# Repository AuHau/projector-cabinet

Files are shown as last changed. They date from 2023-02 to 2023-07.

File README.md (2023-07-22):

# UST Projector cabinet

> DIY "TV" cabinet project housing a hidden motorized screen and UST (ultra-short-throw) projector in motorized drawer.

Demo vide (https://www.youtube.com/watch?v=b7_Dzy0piuk)

## Features

 - "One-press" setup of the home cinema for watching
 - Home Assistant integration
 - Temperature sensor for monitoring the projector's temperature
 - Fans for cooling the projector
 - Collision monitoring of the drawer
 - OTA firmware updates
 - Remote logging to syslog target

## About the project

From my childhood I have dreamed of my own home cinema. About two years ago I have 
decided to embark on an adventure to slowly built it. Since we lived at that moment 
in small flat and planned to move some time soon, creating dedicated "room based" setup was not an 
option. It was around that time that I discovered Ultra Short Throw (UST) projectors
that would match all my requirements and slowly an idea started to grow in my head:

_What if I could place it into a cabinet and have very clean setup with all the components hidden when not using?_

And that is what I have started to work on over weekends and evenings for past 9 months.

Here I plan to share my final design and firmware code for anybody who would like to replicate (and possibly improve on) my work.
I won't be detailing it to the "step-by-step" guide, but leave resources here for people who
know what to do and how to do it.

**I have to warn you though. The project is very tailored to the specific components that I used and describe
later. Any deviation from those components require proper modification of other parameters!**

**Every centimeter makes big difference in the UST projector's screen size and position!**

## Components

 1. UST Projector: [Samsung LSP7T](https://www.samsung.com/uk/projectors/the-premiere/the-premiere-smart-4k-uhd-laser-projector-sp-lsp7tfaxxu/)
 1. Tensioned Floor Screen for UST projects: [Vividstorm S Pro 110"](https://www.vividstorm.eu/products/Vividstorm-S-Pro-110-Electric-Acoustically-Transparent-Floor-Screen-p298146472)
 1. AVR: [Denon X3800H](https://www.denon.com/en-us/product/av-receivers/avr-x3800h/300609-new.html) 
 1. Speakers: 5+1(subwoofer) + 2("Atmos" drivers) from JAMO S809 series
 1. Custom built cabinet from oak
 1. Linear actuator with potentiometer for positional feedback
 1. Control logic board with ESP32

### Cabinet

I am still novice when comes to wood working, so I have decided to leave the build of the
cabinet to my friend cabinetmaker. Therefore, I have design it and modeled it in Fusion 360 
as it was crucial to get the dimensions right because UST projector's viewports are very sensitive 
to any even small deviation and I wanted to obviously maximize the screen's utilization.

This is a render of the model: 

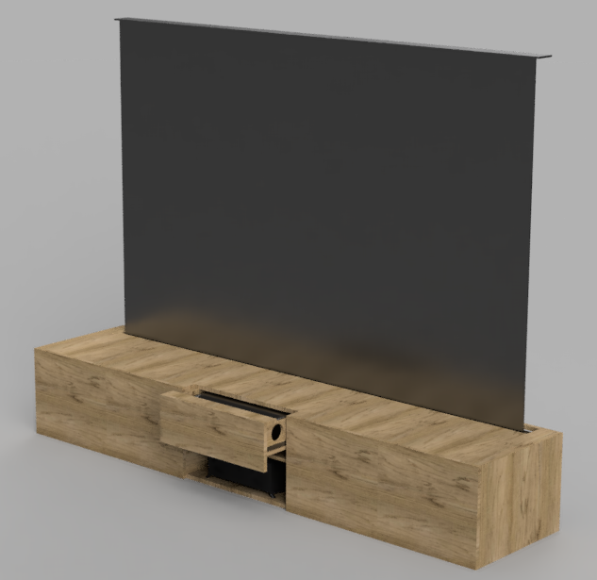
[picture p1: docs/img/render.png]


You can find the Fusion model as file [here](docs/cabinet_model.f3z) or as online model [here](https://uhlir.autodesk360.com/g/shares/SH9285eQTcf875d3c5399135f607261bca4c).
But be aware it is not complete model that could be used as blueprint
for recreating the cabinet! It served more like a mock to understand the dimension requirements.

### Electronics

The brain of the cabinet is custom build circuit around ESP32. I have decided
to program its firmware with MicroPython as Python is close to my heart. The 
circuit serves as integration point of several things:

 - controlling the linear actuator that opens/closes the projector's cabinet
 - controlling USB radio stick of the motorized screen (it works in simple way, if there is power going to the stick than screen is opened, otherwise it closes)
 - controlling the additional PC Fans mounted in the back of the projector's cabinet as otherwise the projector overheats
 - exposing temperature information about the projector

Originally my design goal was to have self-contained circuit. Later on, I have
deviated from this goal as I have decided to scratch my original approach for 
triggering openning/closing the cabinet using monitoring of the AC power line
to the projector and doing decision based on the current passing through that line.

I have instead opted to expose the above functionalities as Home Assistant entities and use the Home Assistant integration to Samsung's Tizen 
that runs on the projector for triggering the proper actions. 
Unfortunately it is not so reliable as sometimes the events from Tizen are not triggered or are triggered multiple times.
I had version of the firmware that was ready for the current-sensing approach, so if you would be interested in that
have a look on [this commit](https://github.com/AuHau/projector-cabinet/commit/b25f13ab9c904240c6eca4cdfa69838080070a1d). 
But be aware even though it was functional, it was not properly tested and finished.

The final schema which includes also the component for measuring the projector's line current mentioned above is here:

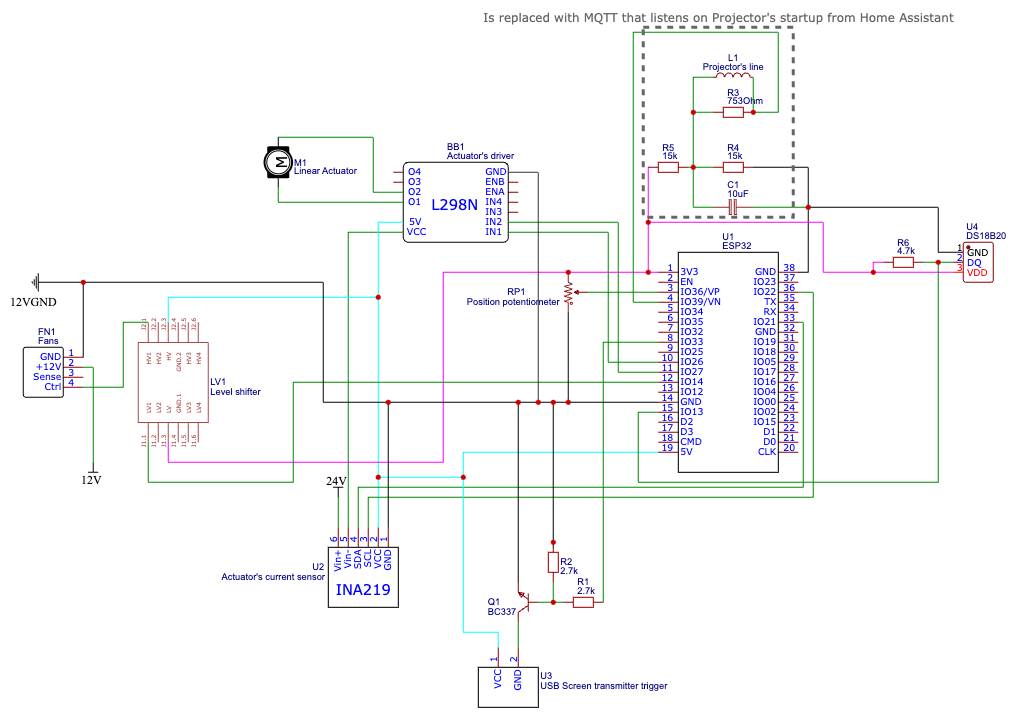
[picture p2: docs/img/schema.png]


You can download its export from EasyEDA [here](./docs/easda-schema.json).

Some pictures of prototyping and final assembly:

<table width="100%">
  <tr>
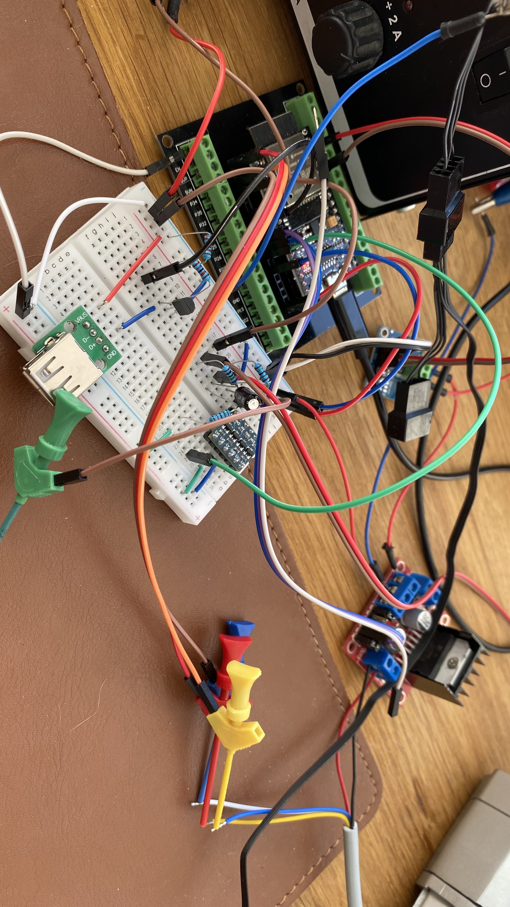
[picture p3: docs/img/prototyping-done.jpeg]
  <td width="50%">  </td>
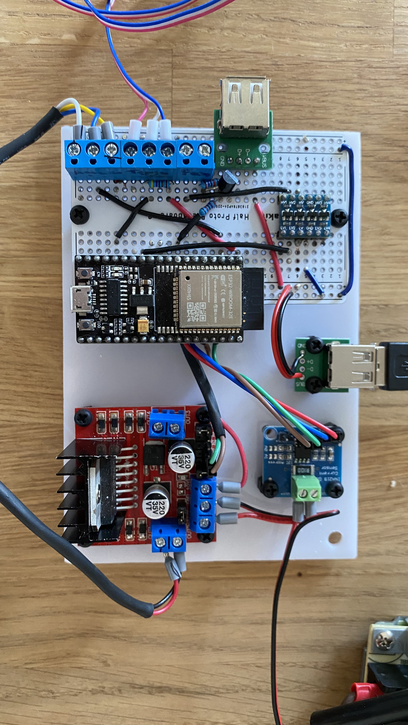
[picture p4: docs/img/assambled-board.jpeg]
  <td width="50%"> </td>
  </tr>
  <tr>
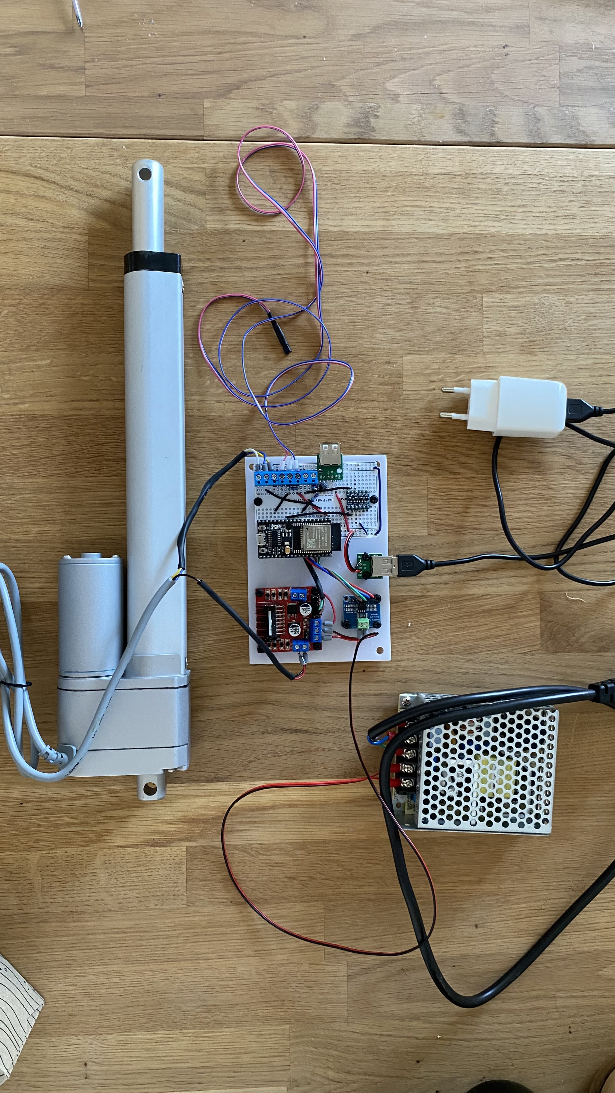
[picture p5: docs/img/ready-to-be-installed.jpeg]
  <td width="50%"></td>
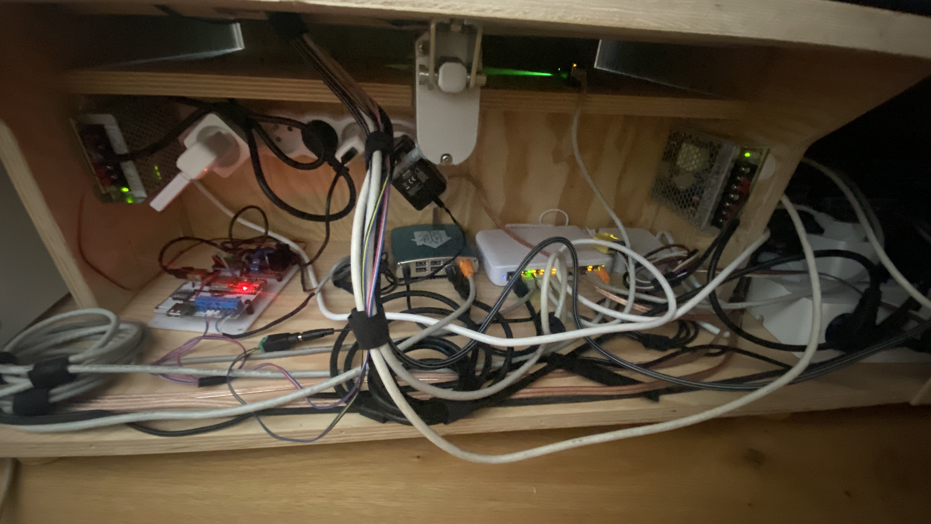
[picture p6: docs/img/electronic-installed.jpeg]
  <td width="50%"></td>
  </tr>
</table>

## Home Assistant

This project heavily relies on Home Assistant for orchestration and integration. Bellow you can see the overview and
capabilities that are exposed over Home Assistant:

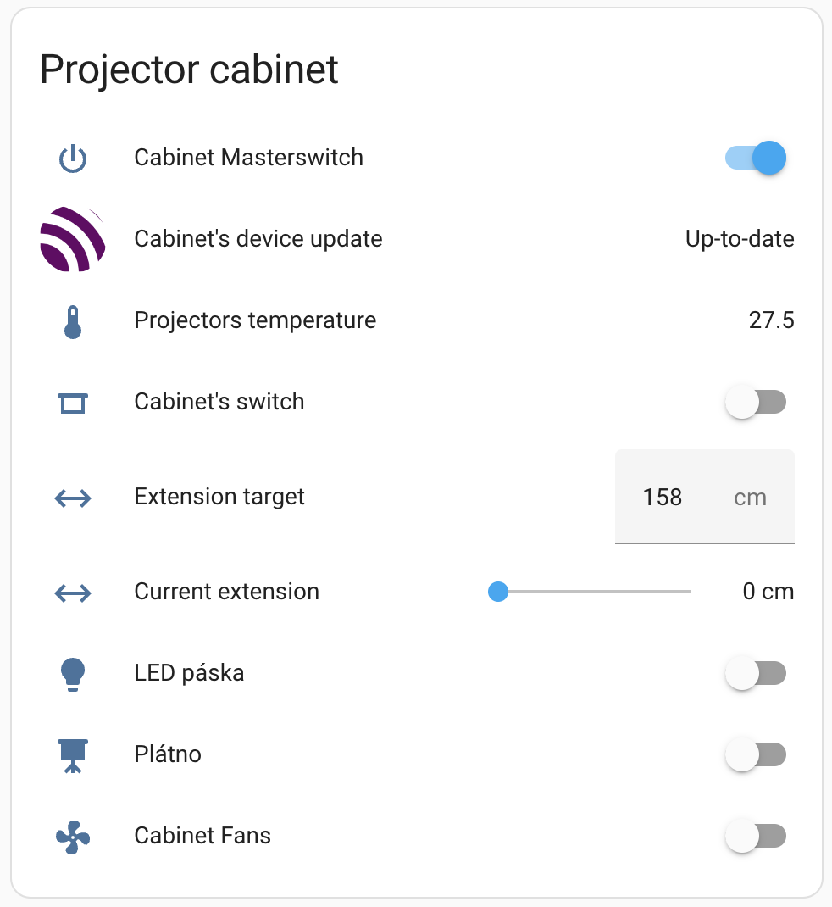
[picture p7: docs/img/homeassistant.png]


## Reproducing the project

As I said I won't provide "step-by-step" guideline here, but here are some pointers for reproducing this, mainly related
to firmware.

### Configuration

Fork this repo. The important configuration needs to be placed in `/app/secrets.py` file. This
file should not be commited (and is currently in `.gitignore`) as it contains sensitive configuration. This configuration
will be persisted over OTA updates. Content of this file shoudl be:

```python
# WiFi settings
WIFI_SSID = "" # YOUR WIFI NAME
WIFI_PASS = "" # YOUR WIFI PASSWORD

# MQTT settings
MQTT_BROKER = "" # NODE WHERE YOU RUN HOME-ASSISTANT'S MQTT
MQTT_USER = ""
MQTT_PASS = ""

# Syslog logging
SYSLOG_HOST = "" # NODE WHERE YOU RUN SYSLOG COLLECTOR
SYSLOG_PORT = ""
```

### OTA updates

OTA updates are sourced from GitHub Releases. For creating those there is Release-Please action which creates
Release PR that when you merge it create new release. With the new release a new firmware resource is build
with CI, which compiles the Python files `.py` into [`.mpy` files](https://docs.micropython.org/en/latest/reference/mpyfiles.html). 

For updating the firmware you need to press in Home Assistant "Install" button on the Firmware entity.

You need to point for the OTA updates to your forked repo in the `/main.py` file you need to tweak the `OTA_REPO` variable.

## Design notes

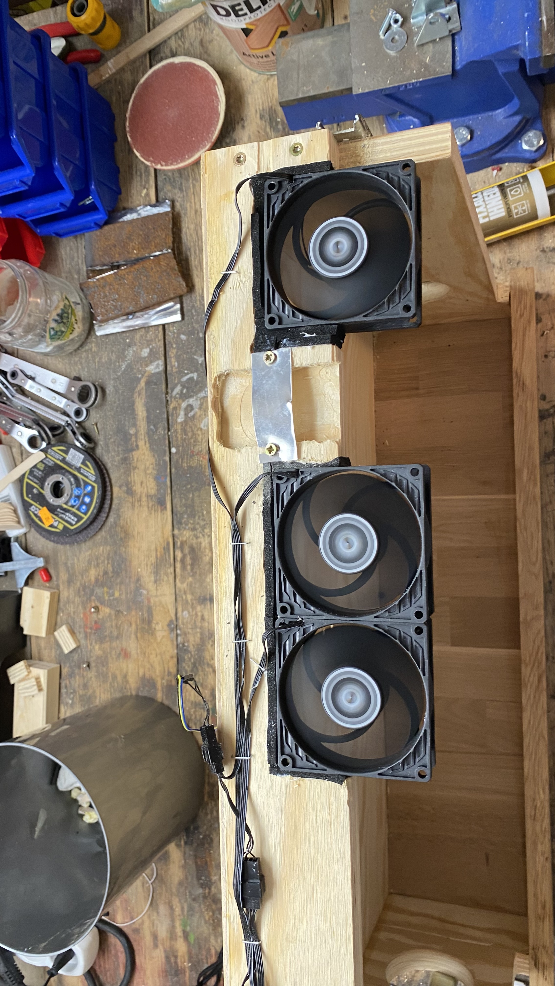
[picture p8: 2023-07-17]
docs/img/fans.jpeg

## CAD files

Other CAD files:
docs/cabinet_model.f3z

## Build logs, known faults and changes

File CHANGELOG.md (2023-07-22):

# Changelog

## [0.3.2](https://github.com/AuHau/projector-cabinet/compare/v0.3.1...v0.3.2) (2023-07-22)

### Bug Fixes

* some more fixing ([0126693](https://github.com/AuHau/projector-cabinet/commit/0126693fc49ac88e7b52665757672bb9edbba45f))
* traceback for unhandled exceptions ([87618a4](https://github.com/AuHau/projector-cabinet/commit/87618a41633968a7fd9db245ec9cdd786ce4bce1))

## [0.3.1](https://github.com/AuHau/projector-cabinet/compare/v0.3.0...v0.3.1) (2023-06-19)

### Bug Fixes

* underflow of fan pwm ([eb5e9b9](https://github.com/AuHau/projector-cabinet/commit/eb5e9b9d5d2ecf6da5a343ec5694fcccc4ab3049))

## [0.3.0](https://github.com/AuHau/projector-cabinet/compare/v0.2.1...v0.3.0) (2023-06-19)

### Features

* **mqtt:** expose actuator's extension ([5a29ce4](https://github.com/AuHau/projector-cabinet/commit/5a29ce446627cf0632ab04ef4f666a7cec7c00e0))

### Bug Fixes

* recover correct configuration when restarting after crash ([5ed0ff6](https://github.com/AuHau/projector-cabinet/commit/5ed0ff681734d7d25988c2870c71c69acecf9d1b))
* syslog format ([484e1cb](https://github.com/AuHau/projector-cabinet/commit/484e1cbc50b07813cca8b98dd84b1062b6938779))

## [0.2.1](https://github.com/AuHau/projector-cabinet/compare/v0.2.0...v0.2.1) (2023-06-18)

### Bug Fixes

* bugs ([7dee334](https://github.com/AuHau/projector-cabinet/commit/7dee334d7eafd5650619703c98dbe3d5649d6b00))

## [0.2.0](https://github.com/AuHau/projector-cabinet/compare/v0.1.5...v0.2.0) (2023-06-18)

### Features

* **mqtt:** extension target configuration ([f5e87b5](https://github.com/AuHau/projector-cabinet/commit/f5e87b5617057703612a36bc812b0418c790dd0a))
* **mqtt:** fans configuration ([5a57b42](https://github.com/AuHau/projector-cabinet/commit/5a57b42f79fea2eea04af359a79ac7d08bdff45d))

### Bug Fixes

* **fan:** off resets duty cycle ([2952681](https://github.com/AuHau/projector-cabinet/commit/2952681409744ba1f1e988e2f01610850ec01ed6))
* revert custom tar and fix tarfile ([b5f4f8b](https://github.com/AuHau/projector-cabinet/commit/b5f4f8b6b115490de6233753be86939c8b0f6fb9))

## [0.1.5](https://github.com/AuHau/projector-cabinet/compare/v0.1.4...v0.1.5) (2023-06-17)

### Bug Fixes

* use different tar compress ([04af35d](https://github.com/AuHau/projector-cabinet/commit/04af35d7a5fc833fdee7b87c0004e570961c3dae))

## [0.1.4](https://github.com/AuHau/projector-cabinet/compare/v0.1.3...v0.1.4) (2023-06-17)

### Bug Fixes

* builded asset source name ([9e7e39e](https://github.com/AuHau/projector-cabinet/commit/9e7e39e49075fb527f5c02b765ce32e60e14f1e8))

## [0.1.3](https://github.com/AuHau/projector-cabinet/compare/v0.1.2...v0.1.3) (2023-06-17)

### Bug Fixes

* builder permissions ([5d11fdc](https://github.com/AuHau/projector-cabinet/commit/5d11fdcc5532be678156ee59be545ae5d648aa9c))

## [0.1.2](https://github.com/AuHau/projector-cabinet/compare/v0.1.1...v0.1.2) (2023-06-17)

### Bug Fixes

* release-please job correct output ([89b9e2e](https://github.com/AuHau/projector-cabinet/commit/89b9e2ed5f7dbc23f5f9cd29d80a6c668b998d48))

## [0.1.1](https://github.com/AuHau/projector-cabinet/compare/v0.1.0...v0.1.1) (2023-06-17)

### Bug Fixes

* merge release jobs ([f4d438b](https://github.com/AuHau/projector-cabinet/commit/f4d438b765b90e49bc31064a78cd9a800a9f87ea))

## [0.1.0](https://github.com/AuHau/projector-cabinet/compare/0.0.1...v0.1.0) (2023-06-17)

### Features

* new OTA mechanism using Github Actions and mpy compiled files ([0b6eb67](https://github.com/AuHau/projector-cabinet/commit/0b6eb67a0d31dac301785eebe84bdcc270f8f68a))

### Bug Fixes

* **ota:** reflect simple release-please type ([7ed303b](https://github.com/AuHau/projector-cabinet/commit/7ed303bbfbd83803e60e727c8198f8a25b256d00))

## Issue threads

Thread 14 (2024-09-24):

Components list

TurboTronix, 2024-09-24:
Great work!

I am looking to make the same but just for the actual UST projector. My screen is static on the wall and the speakers are in wall as well. The amp is in another room.

Do you mind giving a list of the components needed (motor, board, esp module, etc). I'm also using home automation so would be cool to add this with some automations.

AuHau, 2024-09-26:
Thanks :-)

You can find all the components on the electric diagram here: https://github.com/AuHau/projector-cabinet/blob/master/docs/img/schema.png ;-)

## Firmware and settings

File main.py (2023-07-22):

import sys

import uasyncio as asyncio

OTA_REPO = "https://github.com/AuHau/projector-cabinet"


def connect_to_wifi():
    import time, network, gc, app.secrets as secrets
    time.sleep(1)
    print("Bootstrapping")
    print('=> Memory free', gc.mem_free())

    # network.hostname('projector_cabinet')
    wlan = network.WLAN(network.STA_IF)
    print(f"=> WiFi: {'connected - ' + wlan.ifconfig()[0] if wlan.isconnected() else 'NOT connected --> connecting'}")
    if not wlan.isconnected():
        wlan.active(True)
        time.sleep(1)
        wlan.connect(secrets.WIFI_SSID, secrets.WIFI_PASS)
        while not wlan.isconnected():
            pass

    print('=> Network config:', wlan.ifconfig())


def check_for_update():
    import machine, gc
    import ulogging as logging
    from uota import UOta

    print('=> Checking if new firmware version can be installed')
    ota = UOta(OTA_REPO, logger=logging.getLogger('UOta'))
    has_updated = ota.install_new_firmware()
    if has_updated:
        print('=> New version installed! Restarting!')
        machine.reset()
    else:
        del ota
        gc.collect()


def _get_traceback(exception):
    import io, sys
    string_file = io.StringIO()
    sys.print_exception(exception, file=string_file)
    return string_file.getvalue()


def set_global_exception():
    def handle_exception(loop, context):
        import sys, machine
        import ulogging as logging
        exc = context['exception']
        sys.print_exception(exc)
        logging.error(f"Unhandled exception! {exc}")

        formatted_traceback = _get_traceback(exc).replace('\n', ' ==> ')
        logging.debug(f"Traceback: {formatted_traceback}")
        logging.info("Resetting the machine because of unhandled exception.")
        machine.reset()

    loop = asyncio.get_event_loop()
    loop.set_exception_handler(handle_exception)


def start_app():
    print("Sys path: ", ",".join(sys.path))

    from app.main import main
    set_global_exception()  # Debug aid

    return main()


sys.path.append('/app')
sys.path.append('/app/lib')

connect_to_wifi()
check_for_update()

try:
    asyncio.run(start_app())
finally:
    asyncio.new_event_loop()  # Clear retained state

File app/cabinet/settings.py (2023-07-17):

import ujson
import os
from utils import singleton

# Pins settings
TEMP_PIN = 13
USB_TRIGGER_PIN = 33
ACTUATOR_IN1_PIN = 26
ACTUATOR_IN2_PIN = 27
# ACTUATOR_PWM_PIN = 25
POSITION_ADC_PIN = 36
ACTUATOR_CURRENT_SCL_PIN = 22
ACTUATOR_CURRENT_SDA_PIN = 21
FAN_PWM_PIN = 14

"""
Defines the maximal extension of the actuator's arm.
In millimeters.
"""
ACTUATOR_LENGTH = 200

PERSISTENT_SETTINGS_PATH = '/data/setting.json'


@singleton
class PersistentSettings:
    actuator_target = 100
    """
    Target to where the actuator will go when Cabinet is turned on. 
    """

    actuator_obstacle_sma_window = 10
    """
    Number of readings for the Simple Moving Average Window for the obstacle detection of actuator
    """

    actuator_obstacle_max_value_coefficient = 1.32
    """
    Defines limit of max. values accepted to the SMA window
    as a `actuator_obstacle_current * actuator_obstacle_max_value_coefficient`
    """

    actuator_obstacle_current = 600
    """
    The limit current that when actuator reaches it is most likely that there
    is some obstacle. Therefore the actuator will stop and reverse a bit. 
    """

    actuator_obstacle_reverse_distance = 12
    """
    When obstacle is detected then how much actuator should reverse in millimeters.
    """

    actuator_current_monitoring_interval = 100

    projector_number_of_samples = 1484
    """
    Number of samples that is taken for the current reading before reaching the final value
    """

    projector_reading_interval_ms = 500
    """
    How often is current retrieved
    """

    projector_calibration = 0.0415
    """
    Calibration value of the current sensor
    """

    projector_sma_window = 4
    """
    Number of readings for the Simple Moving Average Window
    """

    def __init__(self):
        try:
            os.stat(PERSISTENT_SETTINGS_PATH)
            with open(PERSISTENT_SETTINGS_PATH) as f:
                self._booting = True
                data = dict(ujson.load(f))
                for key, value in data.items():
                    setattr(self, key, value)
                self._booting = False
                print("=> Loaded setting: ", data)
        except OSError:
            print("=> No settings loaded")

    def __setattr__(self, key, value):
        super().__setattr__(key, value)

        try:
            if self._booting or key == '_booting':
                return
        except AttributeError:
            pass

        try:
            os.mkdir('/data')
        except OSError:
            pass

        with open(PERSISTENT_SETTINGS_PATH, mode='w') as f:
            ujson.dump(self.__dict__, f)

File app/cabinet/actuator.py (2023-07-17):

import machine
import uasyncio as asyncio
import ulogging as logging
import aadc

from ina219 import INA219
from utils import singleton
from cabinet import settings

# In ADC reading unit; defines the target range
ADC_PRECISION = 40
CURRENT_SENSOR_SHUNT_OHMS = 0.1
ACTUATOR_TIMEOUT = 20_000  # In milliseconds
MAX_ADC_VALUE = pow(2, 16)


def _convert_actuators_extension_to_adc(goal):
    return goal / settings.ACTUATOR_LENGTH * MAX_ADC_VALUE


def _convert_from_adc_to_actuators_extension(reading):
    return reading / MAX_ADC_VALUE * settings.ACTUATOR_LENGTH


def enum(**enums):
    return type('Enum', (), enums)


MovingDirection = enum(NONE='nowhere', FORWARD='forward', BACKWARD='backward')


def _reverse_moving_direction(value):
    if value == MovingDirection.NONE:
        return MovingDirection.NONE
    elif value == MovingDirection.FORWARD:
        return MovingDirection.BACKWARD
    elif value == MovingDirection.BACKWARD:
        return MovingDirection.FORWARD
    else:
        raise ValueError("Unknown state!")


@singleton
class Actuator:
    def __init__(self):
        self._moving_direction = MovingDirection.NONE
        self._log = logging.getLogger('Actuator')
        self._log_obstacle = logging.getLogger('Actuator:ObstacleDetection')
        self._settings = settings.PersistentSettings()
        self._avoiding_obstacle = False

        self.position_adc_pin = machine.ADC(machine.Pin(settings.POSITION_ADC_PIN), atten=machine.ADC.ATTN_11DB)
        self.position_adc = aadc.AADC(self.position_adc_pin)
        self.position_adc.sense(False)  # Will make it to wait until the reading is in given range

        self.in1 = machine.Pin(settings.ACTUATOR_IN1_PIN, machine.Pin.OUT)
        self.in2 = machine.Pin(settings.ACTUATOR_IN2_PIN, machine.Pin.OUT)
        self.in1.off()
        self.in2.off()

        i2c = machine.SoftI2C(machine.Pin(settings.ACTUATOR_CURRENT_SCL_PIN),
                              machine.Pin(settings.ACTUATOR_CURRENT_SDA_PIN))
        self.current_sensor = INA219(CURRENT_SENSOR_SHUNT_OHMS, i2c, log_level=logging.WARNING)
        self.current_sensor.configure()

    def start(self):
        asyncio.create_task(self._log_values())

    def is_extended(self):
        return self.position_adc_pin.read_u16() > ADC_PRECISION

    def get_position(self):
        return _convert_from_adc_to_actuators_extension(self.position_adc_pin.read_u16())

    async def go_back(self):
        self._log.info("Going back")
        return await self.go_to(0)

    async def go_to(self, target):
        """
        Returns boolean which indicates if actuator reached the original target (true)
        or had to do obstacle avoidance (false)
        """
        did_obstacle_avoidence = False
        try:
            finished_move_event = asyncio.Event()
            while not finished_move_event.is_set():
                move_task = asyncio.create_task(self._go_to(target, finished_move_event))

                # _detect_obstacle cancels the move_task when obstacle is detected and specifies
                # the new target value for the move
                target = await asyncio.wait_for_ms(self._detect_obstacles(finished_move_event, move_task),
                                                   ACTUATOR_TIMEOUT)

                if target is None:
                    break
                else:
                    did_obstacle_avoidence = True
        except asyncio.TimeoutError:
            self._log.warning("The go_to routine timed out!")
        finally:
            # We might or might not have been avoiding obstacles, but lets reset it to default value
            # at the end of the move just as precaution, so it is ready for future moves!
            self._avoiding_obstacle = False

        return not did_obstacle_avoidence

    async def _go_to(self, target, finished_event):
        current_position = _convert_from_adc_to_actuators_extension(self.position_adc_pin.read_u16())
        where_to_move = MovingDirection.FORWARD if target > current_position else MovingDirection.BACKWARD
        adc_target = _convert_actuators_extension_to_adc(target)

        self._log.info(
            f"Going to target {target}mm. Current position {current_position}mm ==> Moving {where_to_move.upper()}")

        if where_to_move == MovingDirection.FORWARD:
            self._go_forward()
            await self.position_adc(adc_target - ADC_PRECISION, MAX_ADC_VALUE)
        elif where_to_move == MovingDirection.BACKWARD:
            self._go_back()
            await self.position_adc(0, adc_target + ADC_PRECISION)

        self._log.debug(f"Finished the move {current_position}mm --> {target}mm")
        self._stop()
        finished_event.set()

    def _go_forward(self):
        self._moving_direction = MovingDirection.FORWARD
        self.in1.on()

    def _go_back(self):
        self._moving_direction = MovingDirection.BACKWARD
        self.in2.on()

    def _stop(self):
        self._log.info("Stopping")
        self._moving_direction = MovingDirection.NONE
        self.in1.off()
        self.in2.off()

    def _get_obstacle_target(self, current_move_direction):
        target_retraction = _convert_from_adc_to_actuators_extension(self.position_adc_pin.read_u16())
        if current_move_direction == MovingDirection.FORWARD:
            target_retraction -= self._settings.actuator_obstacle_reverse_distance
        elif current_move_direction == MovingDirection.BACKWARD:
            target_retraction += self._settings.actuator_obstacle_reverse_distance
        else:
            self._log_obstacle.error("We should be avoiding obstacle but we are not moving!")

        if target_retraction < 0:
            return 0

        if target_retraction > settings.ACTUATOR_LENGTH:
            return settings.ACTUATOR_LENGTH

        self._log_obstacle.info(f"Reversing {self._settings.actuator_obstacle_reverse_distance}mm to {target_retraction}mm.")

        return target_retraction

    async def _detect_obstacles(self, finished_move_event, move_task):
        if not self._settings.actuator_obstacle_current:
            self._log_obstacle.warning("Obstacle current is not defined. No obstacle detection is happening.")
            await finished_move_event.wait()
            return

        # SMA = Simple Moving Average
        sma_values = []
        sma_sum = 0

        # We monitor the current only while actuator is moving which is signaled by this event
        while not finished_move_event.is_set():
            current = self.current_sensor.current()
            max_allowed_current = self._settings.actuator_obstacle_max_value_coefficient * self._settings.actuator_obstacle_current

            if current > max_allowed_current:
                current = max_allowed_current

            sma_sum += current
            sma_values.append(current)
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

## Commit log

2023-02-25 feat: somewhat working obstacle avoidence
    [actuator.py, cabinet.py, settings.py]
2023-03-07 feat: filter spike current values from sma
2023-03-21 feat: usb trigger pin
2023-03-27 feat: projector on off current detection
2023-03-29 feat: fan support
2023-05-05 feat: temperature sensor
2023-06-17 ci: fix build flow typos
2023-06-18 fix(fan): off resets duty cycle
    [fan.py]
2023-06-19 fix: recover correct configuration when restarting after crash
    [actuator.py, cabinet.py]
2023-06-19 feat(mqtt): expose actuator's extension
2023-06-19 fix: underflow of fan pwm
    [fan.py]
2023-07-17 fix: some more fixing
    [actuator.py, fan.py, mqtt.py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]
2023-07-17 docs: readme
    [cabinet_model.f3z]
2023-07-22 fix: traceback for unhandled exceptions
    [main.py]
2023-08-15 fix: crash recovery when cabinet is expanded bug
    [cabinet.py]
